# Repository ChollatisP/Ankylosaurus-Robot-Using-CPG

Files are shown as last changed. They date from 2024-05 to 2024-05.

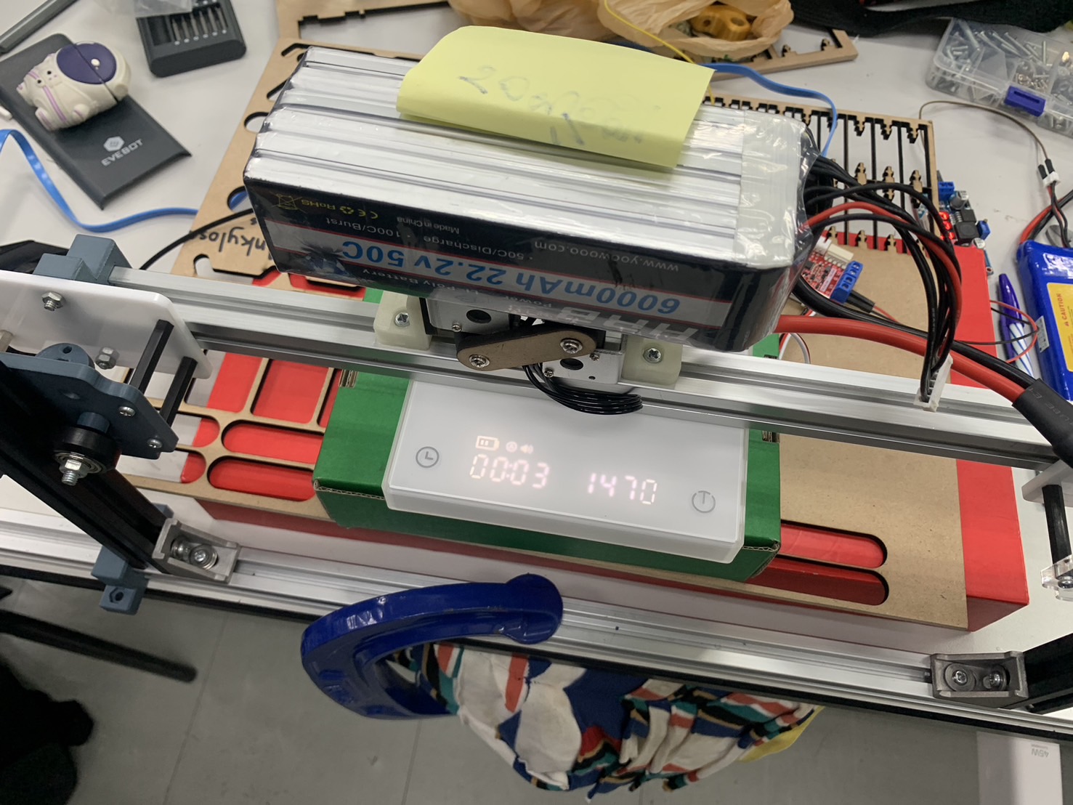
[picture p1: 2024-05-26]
Prove/Weight_test.jpg

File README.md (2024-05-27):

# Ankylosaurus Robot

## Description

The goal of this Mini-Project is to design and develop a robotic system inspired by the Ankylosaurus, an armored dinosaur. This robot will utilize a Central Pattern Generator (CPG), Virtual Rhythmic Networks (VRNs), and Virtual Hormones to simulate the nervous system found in living organisms. 

## Table of Content
- Ankylosaurus-Robot-Using-CPG
  - Description
  - Table of Content
  - Concept
    - Hormone
    - CPG-VRN
    - Robot design
  - Part
    - Tail
    - Neck-Head
    - Body
    - Left-Rear-Leg
    - Right-Rear-Leg
    - Left-Front-Leg
    - Right-Front-Leg
  - Assembly
  - Component
    - Software
    - Hardware
    - Installation
  - Authors
  - Acknowledgments
    - Manual and Datasheet
    - Reference

## Concept

### - CPG and VRN

<p align="center">
  
</p>
  
The robotic system, inspired by an ankylosaurus, features shoulder joints (M0-M3) and knee joints (M4-M7). SO2 is employed with O1 and O2 as outputs. Output from O1 controls knee joints, with weights of 1 and -1 causing Front Left and Rear Right knees to move in sync, while Front Right and Rear Left knees move oppositely, mimicking ankylosaurus limb coordination. Additionally, output from O2 is combined with Input 1 and 2 to allow inputs to influence shoulder movement, termed VRNs (Variable Response Networks), enabling input values to affect robot motion. 

### - Hormone

<p align="center">
  
</p>

In our hormone system, we use the motor torque to represent the robot's fatigue. We calculate the sum of the servo torque over five time windows and determine the standard deviation (SD) of this torque. This SD is then used in the hormone equation:

Hc[t]=(a⋅SD(Torque))+(b⋅Hc[t−1])

where 
a (alpha) and 
b (beta) are constants. The output 
Hc from this equation is used to adjust the motor speed. This system allows the hormone levels to influence the walking speed of the robot.

### - Robot design

* Materials and Equipment
  - PLA
  - Acrylic,2 mm and 4 mm
  - Wooden board 4 mm
  - Bearing(623RS) 3 mm
  - Screw
  - Nut
  - Inner tube
  - PVC pipe

* Body
  * Reference
    <p align="center">
      
    </p>

  * After choosing the Ankylosaurus as a reference for our robot, we based our design on a four-legged animal. Studying the skeleton of the Ankylosaurus, which has different leg lengths, we designed the front legs to be 86 centimeters long and the rear legs to be 115 centimeters long.

  * Free body diagram and Calculate force max in the home position. [Click hear](https://github.com/ChollatisP/Ankylosaurus-Robot-Using-CPG/blob/main/Prove/Free_body_diagram.pdf)
  * Experiment
    * Design testing showed that one leg can support 1500 grams, allowing the robot to support a total weight of 3000 grams with two legs. The robot's overall weight is approximately 1500 grams, with a tolerance of up to 50 percent (or 1500 grams). [Click hear](https://github.com/ChollatisP/Ankylosaurus-Robot-Using-CPG/blob/main/Prove/Experiment.mp4)
    * Energy consumption. [Click hear](https://github.com/ChollatisP/Ankylosaurus-Robot-Using-CPG/blob/main/Prove/Battery_Calculation.pdf)

* Tail
  * Reference
    <p align="center">
      
      
    </p>
    
  * We design 3D-printable joints for assembling a tail using PLA filament, with a total weight of 36 grams. Drawing inspiration from dragon models, the joints feature a grab mechanism, enabling the tail to move left and right.

* Head
  * Reference
    <p align="center">
      
      
    </p>

  * We designed the head structure based on Ankylosaurus anatomy. Its structure is similar to that of a turtle. But it has sharp spines and bone-like armor to protect it from predators. We also designed the mouth to have a jaw-like structure. This allows the servo to control the movement of the mouth. It also has a long neck so that the servo can move the neck up and down.

## Part

### - Tail

<p align="center">
  
</p>

### - Neck-Head

https://github.com/ChollatisP/Ankylosaurus-Robot-Using-CPG/assets/154317545/061143af-20ef-42ed-8587-2f487bc01352

### - Body

https://github.com/ChollatisP/Ankylosaurus-Robot-Using-CPG/assets/154317545/31a39d6f-0629-42f6-9094-0288651878a0

### - Left-Rear-Leg

https://github.com/ChollatisP/Ankylosaurus-Robot-Using-CPG/assets/154317545/f0d755fc-a621-4187-81f4-3e616c87f374

### - Right-Rear-Leg

https://github.com/ChollatisP/Ankylosaurus-Robot-Using-CPG/assets/154317545/73323a92-11e0-47a3-b45a-8f9a36d1330e

### - Left-Front-Leg

https://github.com/ChollatisP/Ankylosaurus-Robot-Using-CPG/assets/154317545/a362d214-d938-400e-98b1-ab38c1122920

### - Right-Front-Leg

https://github.com/ChollatisP/Ankylosaurus-Robot-Using-CPG/assets/154317545/f60c23ce-5cd6-48cf-a238-8bfbbe61a805

## Assembly

https://github.com/ChollatisP/Ankylosaurus-Robot-Using-CPG/assets/154317545/6cbdc5d4-3189-4b34-b544-ea275060897f

## Component

### - Software

* [Arduino IDE](https://www.arduino.cc/en/software) (Any version)
  * Library
    * Normal
      * math.h
      * WiFi.h
      * PubSubClient.h
      * ESP32Servo.h
      * [How to install arduino library](https://support.arduino.cc/hc/en-us/articles/5145457742236-Add-libraries-to-Arduino-IDE) 

    * Additional

      * [SCS15 Servo arduino driver](https://github.com/IS2511/SCServo.git)

      * [How to install additional arduino library](https://docs.arduino.cc/software/ide-v1/tutorials/installing-libraries/)  

* SOLIDWORKS or Fusion 360 or any cad design software.

* RDWorksV8 (Laser Cut and Engrave Software)

* PrusaSlicer (Up to your 3D printer)

* [Node-RED](https://www.influxdata.com/blog/guide-installing-node-red/)
  * [Palette node-red-dashboard](https://www.influxdata.com/blog/node-red-dashboard-tutorial/)

* [FD 1.9.8.2](https://github.com/ChollatisP/Ankylosaurus-Robot-Using-CPG/tree/main/Feetech%20SCSservo%20Software) (SCSservo Software)

### - Hardware

* Feetech SCS15 Motor 
   * quantity 8
 * FE-URT-1 
   * quantity 1
 * Step Down (LM2596) 
   * quantity 1
 * MG90S Servo Motor 
   * quantity 2
 * Arduimo UNO R4 WIFI 
   * quantity 1
 * Node32S
   * quantity 1
 * Photo Board (8.5*5.5 cm.)
   * quantity 1
 * 3000 mAh Li-Po Battery
   * quantity 1
 * Jumper wire

### - Diagram & Wiring

<p align="center">
  
  
</p>

### - Installation

<p align="center">
  
</p>

## Group members 

* Nipitpon Phumchoedchan 6452500015

* Chollatis Petchsing 6452500023

* Akaraphon Trakoolwiya 6452500180

* Kantawit Panyateang 6452500198

* Wiraphat panma 6452500350

* Komgrid Petchpayub 6452500392

## Acknowledgments
### - Manual and Datasheet

* [Arduino® UNO R4 WiFi](https://docs.arduino.cc/resources/datasheets/ABX00087-datasheet.pdf)

* [Servo motor SCS 15](https://www.feetechrc.com/Data/feetechrc/upload/file/20201127/start%20%20tutorial201015.pdf)

* [Servo motor SCS 15 manual](https://grobotronics.com/images/companies/1/datasheets/SCS15&SCS115%20Manual.pdf?1516269264467)

* [FE-URT-1](https://www.mantech.co.za/datasheets/products/FE-URT-1%20specs.pdf)

* [Step Down (LM2596)](https://www.ti.com/lit/ds/symlink/lm2596.pdf)

* [MG90S Servo Motor](https://www.electronicoscaldas.com/datasheet/MG90S_Tower-Pro.pdf)

* [Node32S](https://www.es.co.th/Schemetic/PDF/ESP32.PDF)

### - [Reference](https://github.com/ChollatisP/Ankylosaurus-Robot-Using-CPG/tree/main/Reference)

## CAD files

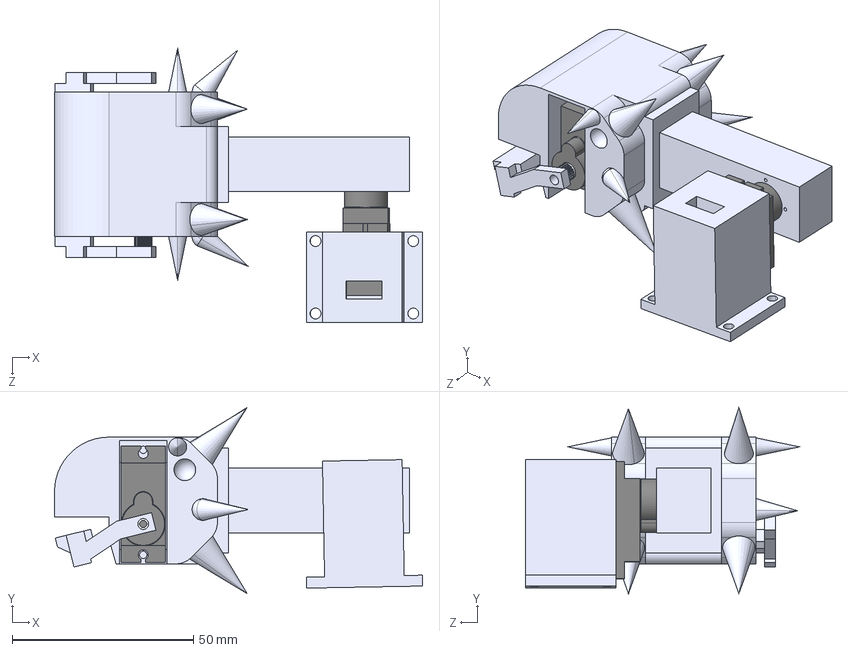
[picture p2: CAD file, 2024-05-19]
CAD/File step/HEAD/Assembly.STEP
101.6 x 51.5 x 75.7 mm
MG90S Servo Motor.stp x 2

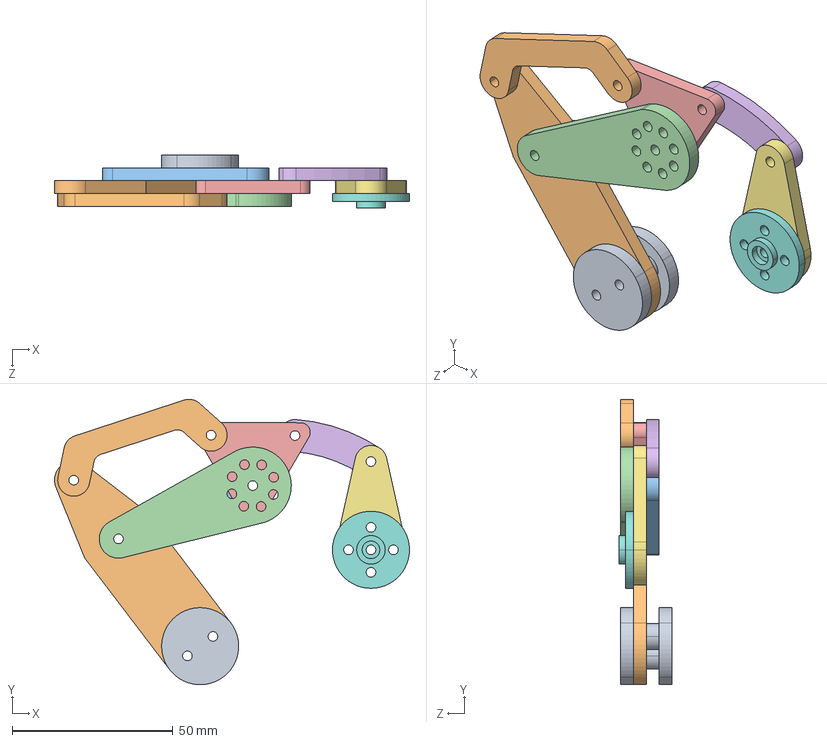
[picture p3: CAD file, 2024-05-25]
CAD/File step/Legs/Front legs/Assembly Right.STEP
110.6 x 88.9 x 16.5 mm
back10.step x 2
front1.step
front2.step
front4.step
front5.step
front6.step
front7.step
front8.step
front9.step x 2
front3.step

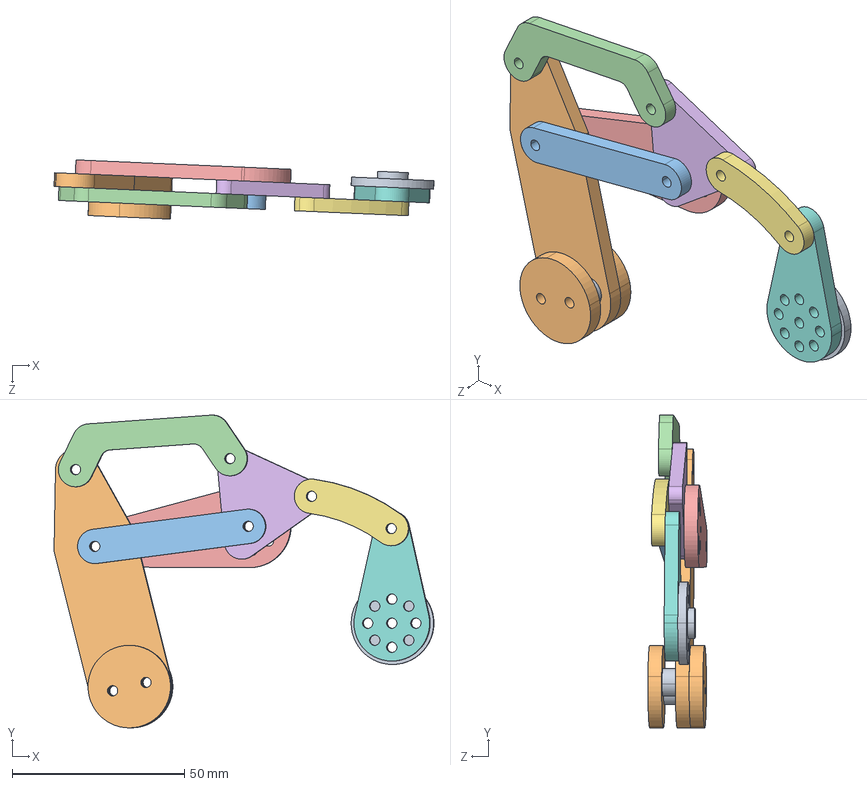
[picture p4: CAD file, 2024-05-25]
CAD/File step/Legs/Front legs/Assembly Left.STEP
110.4 x 90.9 x 17.2 mm
back10.step x 2
front1.step
front2.step
front3.step
front4.step
front5.step
front6.step
front7.step
front8.step
front9.step x 2

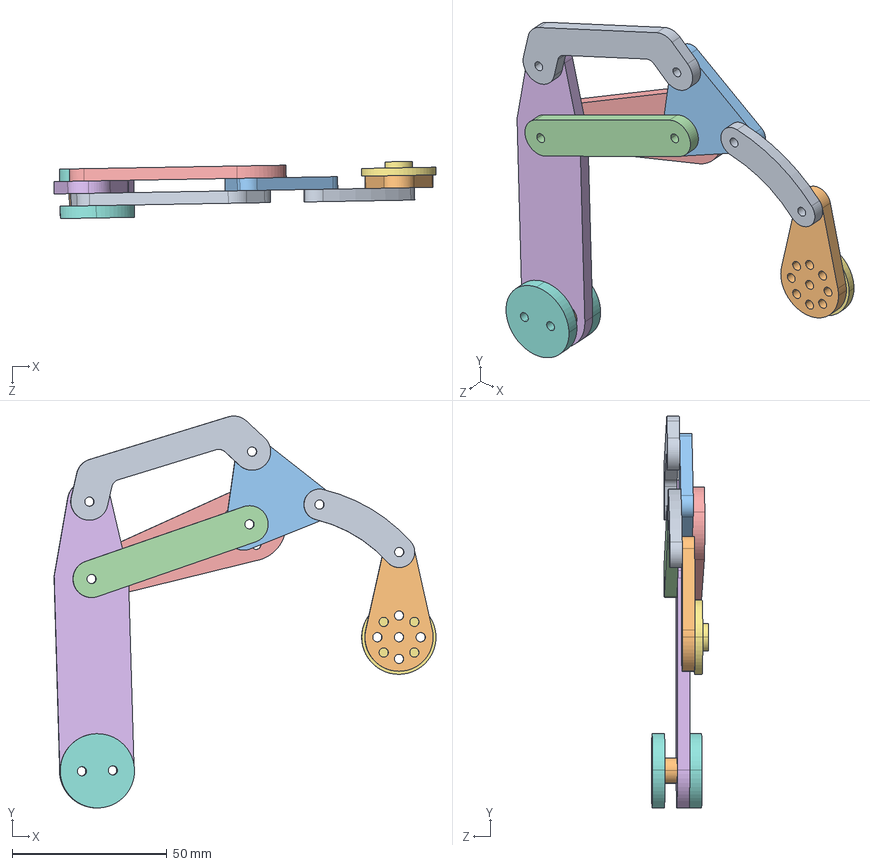
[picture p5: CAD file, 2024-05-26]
CAD/File step/Legs/Rear legs/Assembly Left.STEP
123.4 x 126.6 x 18.5 mm
back1.step
back10.step x 2
back2.step
back3.step
back4.step
back5.step
back6.step
back7.step x 2
back8.step
back9.step

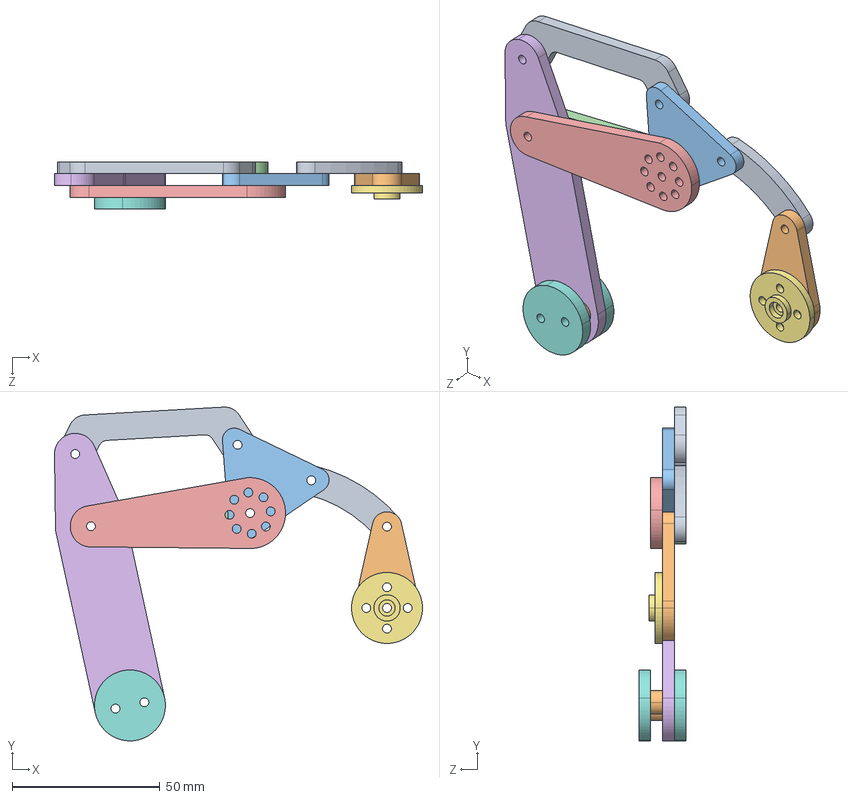
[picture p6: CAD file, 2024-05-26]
CAD/File step/Legs/Rear legs/Assembly Right.STEP
124.4 x 112.9 x 16.0 mm
back1.step
back10.step x 2
back2.step
back3.step
back4.step
back5.step
back6.step
back7.step x 2
back8.step
back9.step

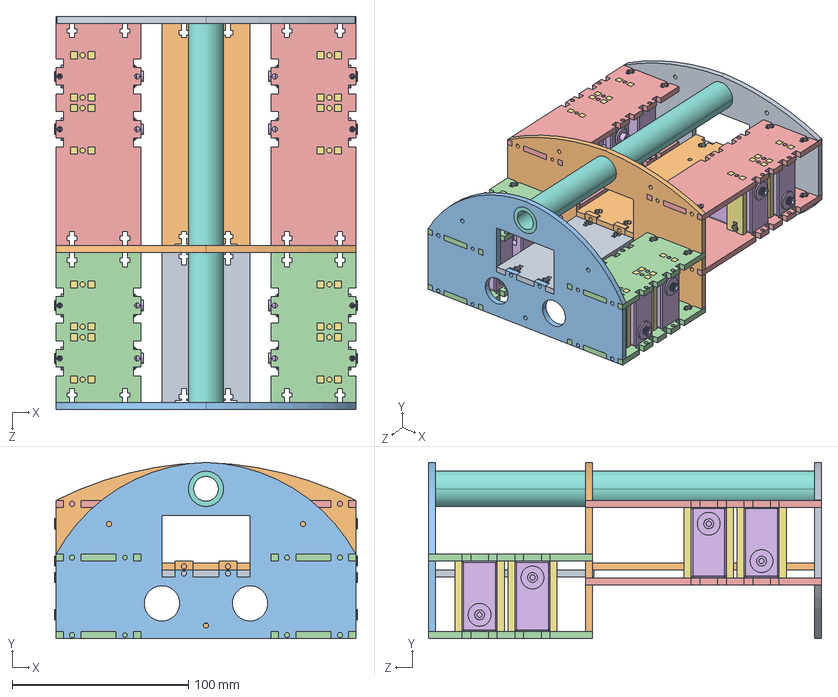
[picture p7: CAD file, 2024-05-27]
CAD/File step/BODY/BodyAssembly.STEP
172.0 x 100.0 x 223.0 mm
หลัง2.4.2
หลัง2.4
หลัง3
servoscs15.step x 8
เเนบมอเตอร์ x 16
ตรงกลาง
ตรงกลาง2.1

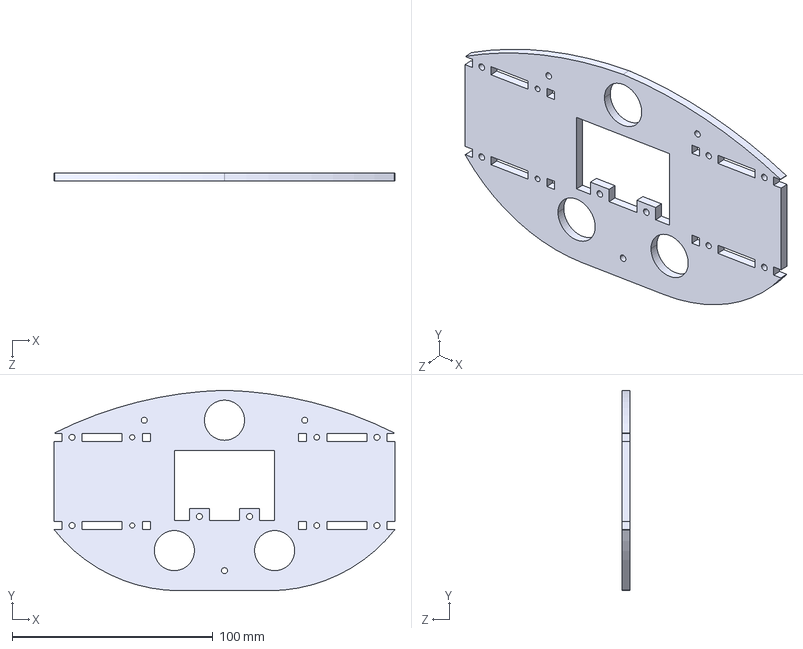
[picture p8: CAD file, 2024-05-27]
CAD/File step/BODY/BODY_PART7.STEP
170.0 x 99.9 x 4.00 mm

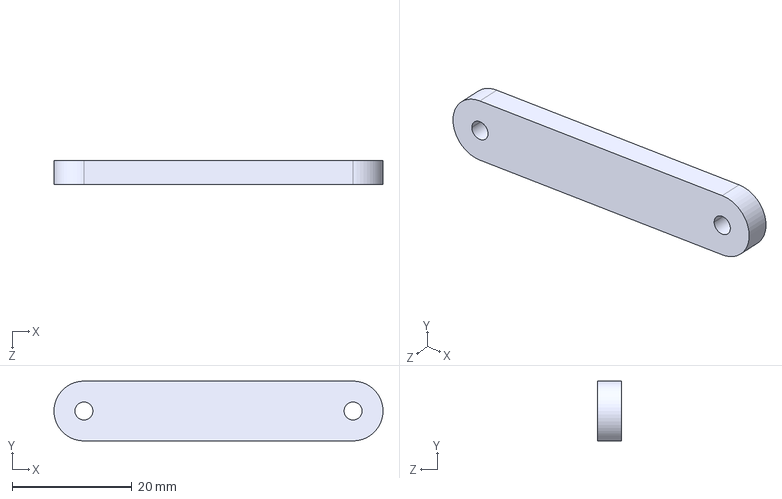
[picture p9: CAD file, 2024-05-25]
CAD/File step/Legs/Front legs/front2.STEP
55.0 x 10.0 x 4.00 mm

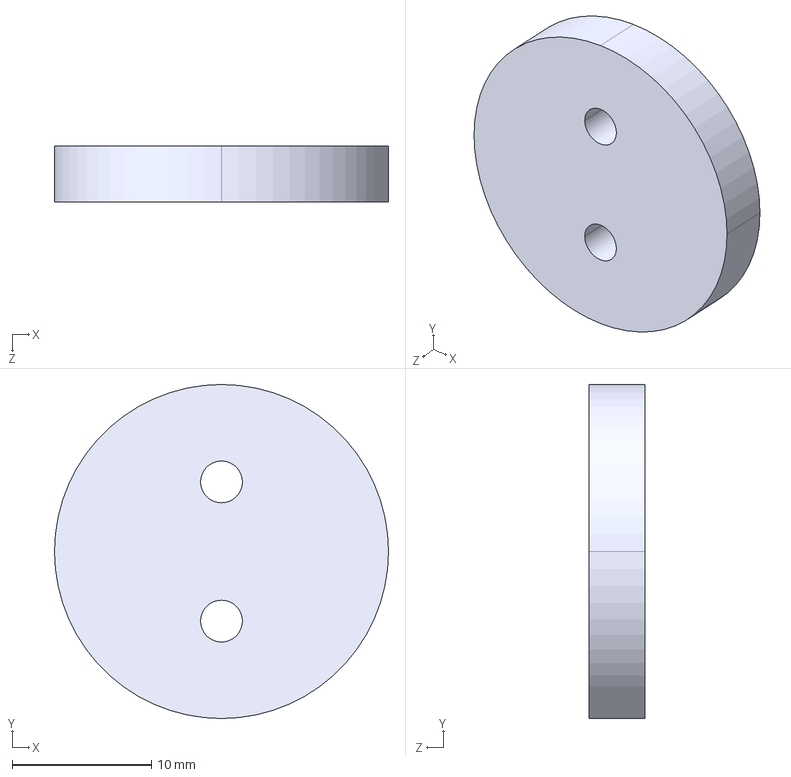
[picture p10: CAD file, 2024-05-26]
CAD/File step/Legs/Rear legs/back7.STEP
24.0 x 24.0 x 4.00 mm

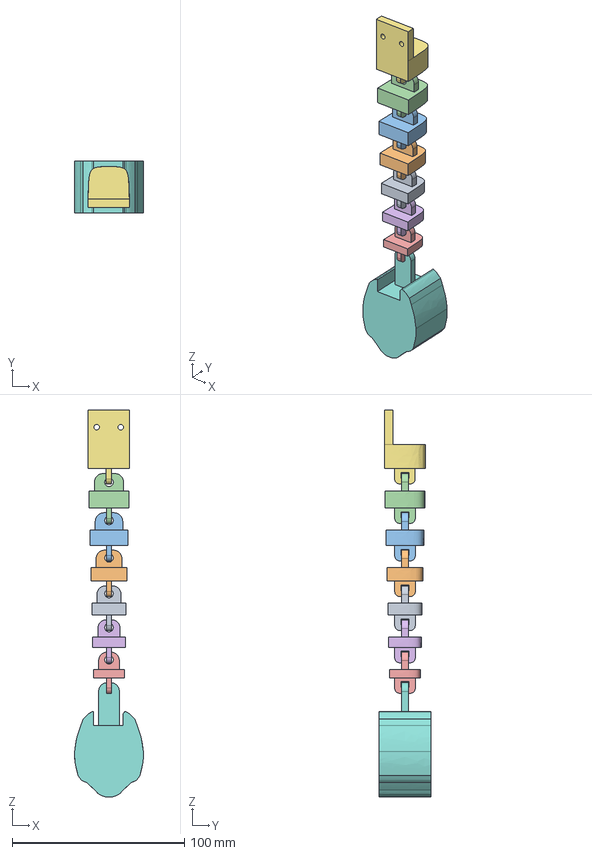
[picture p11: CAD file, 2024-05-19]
CAD/File step/Tail.step
40.0 x 30.0 x 225.0 mm
Test more3
Test more2
Test more1
Test more0
Test more5
Test more4
Test more0.1
Big

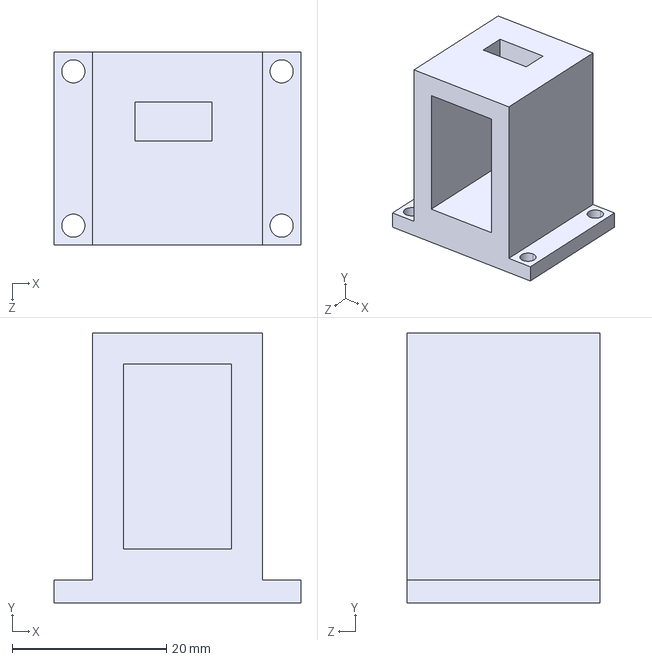
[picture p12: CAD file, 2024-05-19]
CAD/File step/HEAD/Part3.STEP
32.0 x 35.0 x 25.0 mm

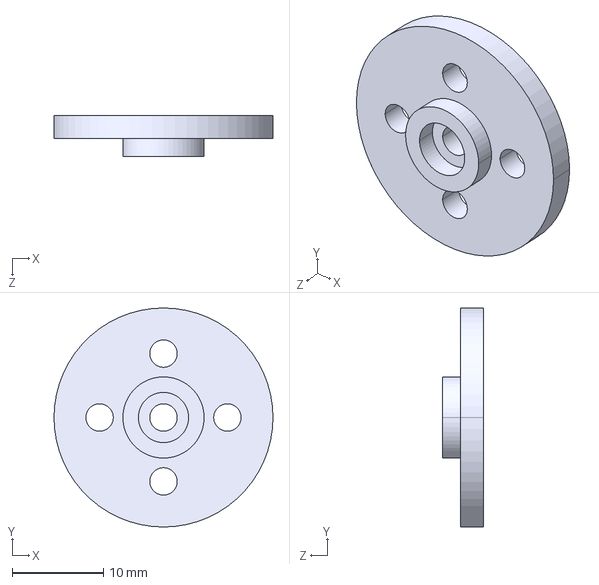
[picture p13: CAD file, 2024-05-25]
CAD/File step/Legs/Front legs/front8.STEP
24.0 x 24.0 x 4.50 mm

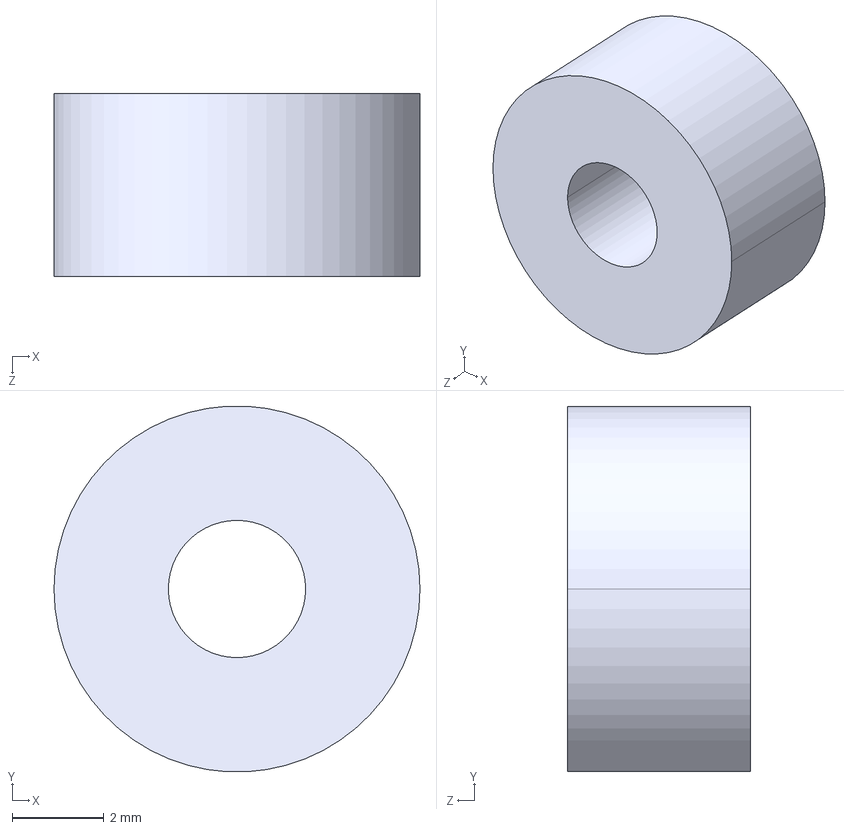
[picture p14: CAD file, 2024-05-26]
CAD/File step/Legs/Rear legs/back10.STEP
8.00 x 7.99 x 4.00 mm

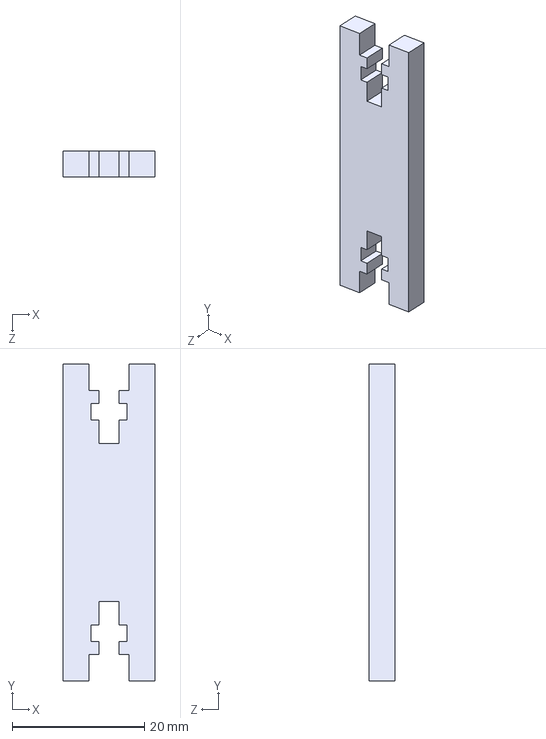
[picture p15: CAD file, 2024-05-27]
CAD/File step/BODY/BODY_PART9.STEP
14.0 x 48.0 x 4.00 mm

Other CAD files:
CAD/File step/BODY/BODY_PART3.STEP
CAD/File step/HEAD/Part5.STEP
CAD/File step/Legs/Rear legs/back1.STEP
CAD/File step/BODY/BODY_PART6.STEP
CAD/File step/BODY/BODY_PART1.STEP
CAD/File step/BODY/BODY_PART2.STEP
CAD/File step/BODY/BODY_PART4.STEP
CAD/File step/BODY/BODY_PART5.STEP
CAD/File step/BODY/BODY_PART8.STEP
CAD/File step/HEAD/Part1.STEP
CAD/File step/HEAD/Part2.STEP
CAD/File step/HEAD/Part6.STEP
CAD/File step/Legs/Front legs/front1.STEP
CAD/File step/Legs/Front legs/front10.STEP
CAD/File step/Legs/Front legs/front3.STEP
CAD/File step/Legs/Front legs/front4.STEP
CAD/File step/Legs/Front legs/front5.STEP
CAD/File step/Legs/Front legs/front6.STEP
CAD/File step/Legs/Front legs/front7.STEP
CAD/File step/Legs/Front legs/front9.STEP
CAD/File step/Legs/Rear legs/back2.STEP
CAD/File step/Legs/Rear legs/back3.STEP
CAD/File step/Legs/Rear legs/back4.STEP
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

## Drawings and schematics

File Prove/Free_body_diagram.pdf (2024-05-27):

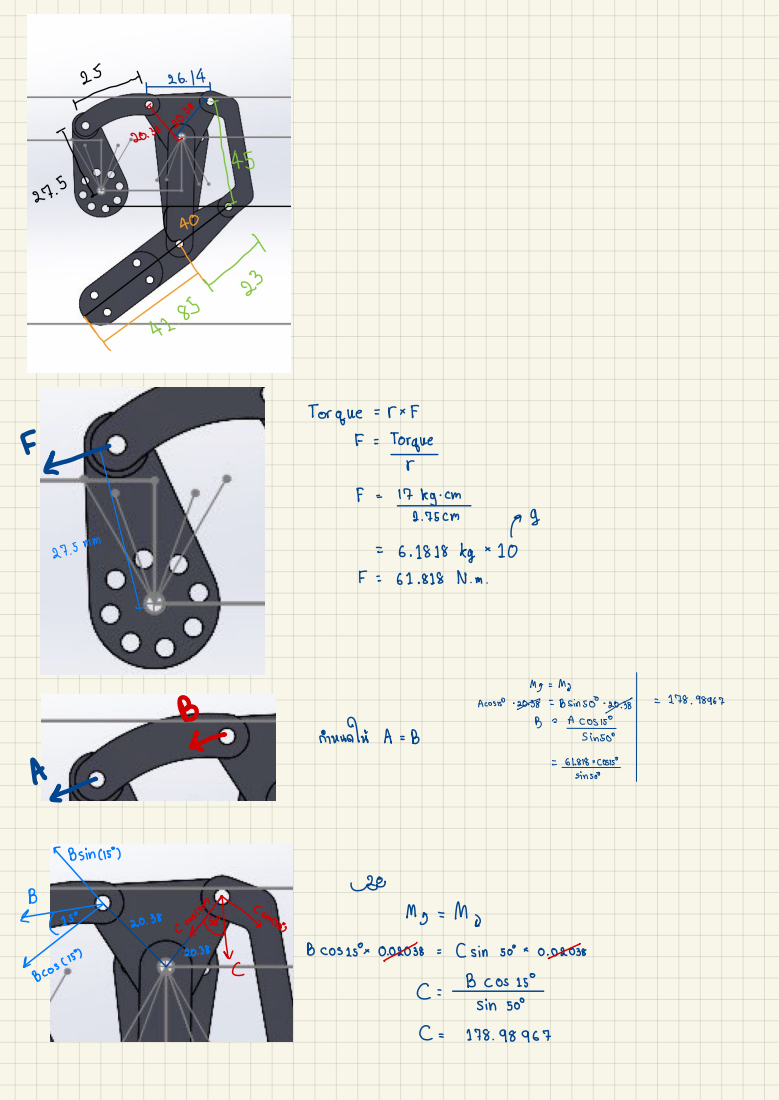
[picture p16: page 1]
Torque =; Torque; F = ·17 Reg. cm; A cOSISO; ·8 = BSinsoO :; กำหนดให้ A =; B = A COSISO; SinSor; - COSISO ↑; sin 50; 5 BSin C15; Sinceo 20.38; COS15,; 0.02038 = ( sin; cos (¹⁵; BCos 13; sin

# Ma = MG

CSinsox0.023 = | Dxsin | 15 x 0.04185

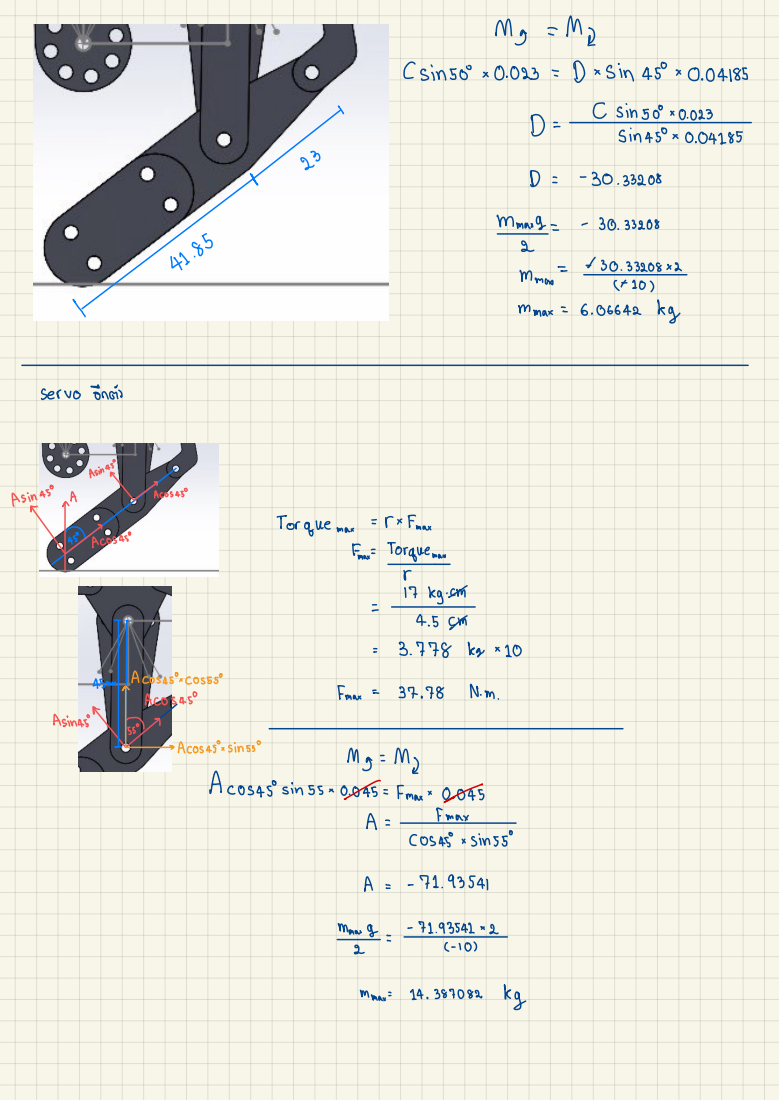
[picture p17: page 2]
sin 500 -; Sin 450 -; - 30.33208 uss "; mmax8 =; mmox; mmax =; servo อีกต; Asin " cos4s Asin ⁴⁵·A ↑; Accos 49; Torque max =; Ux Fmax; Emax =; Torque max; keg. =; ACOS450 , COS550 ค; ACOS 45; Frax =; Asinas &; · ACOS45-; sings; Mar = MG; ACOS4S sin 5 3 -; 0 = Fmax - 0.045 -; I max; COS45 + Sins %; mmas 8 -=; mmax=

| 30 | -
↳ | (25% | 23.48 %

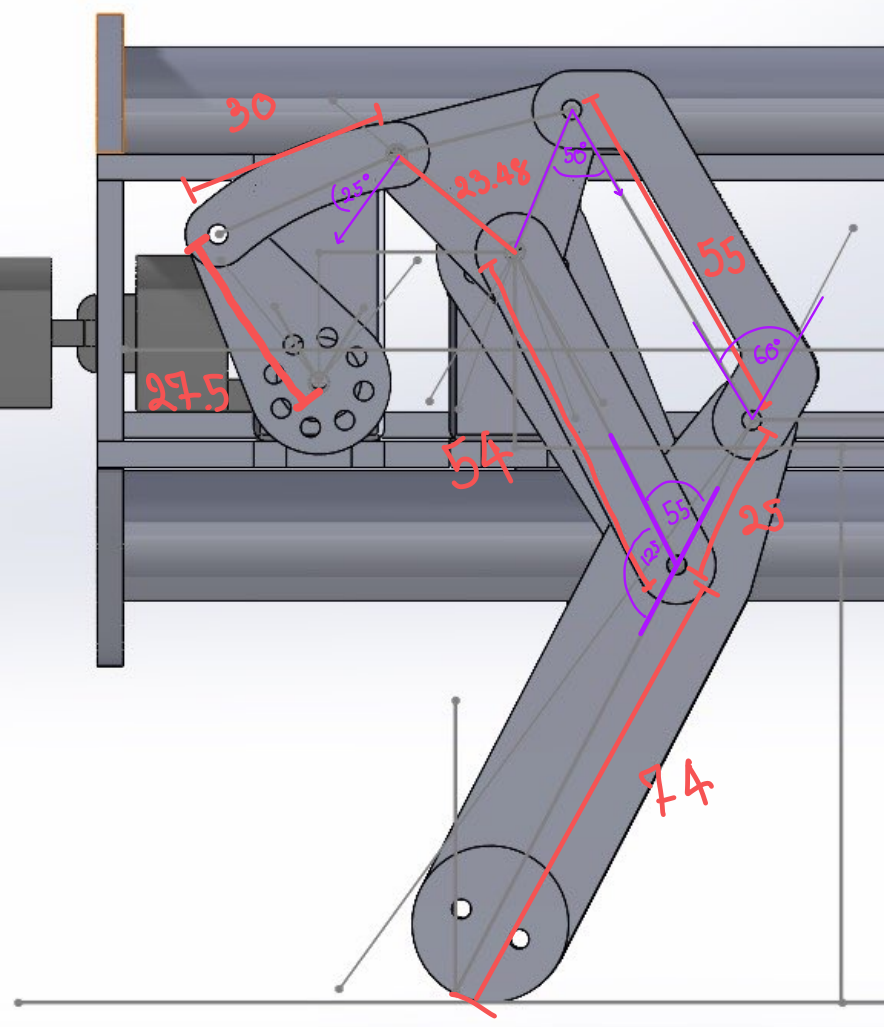
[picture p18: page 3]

MACOSASO รีว | docos | 8Bsin40
pr | -

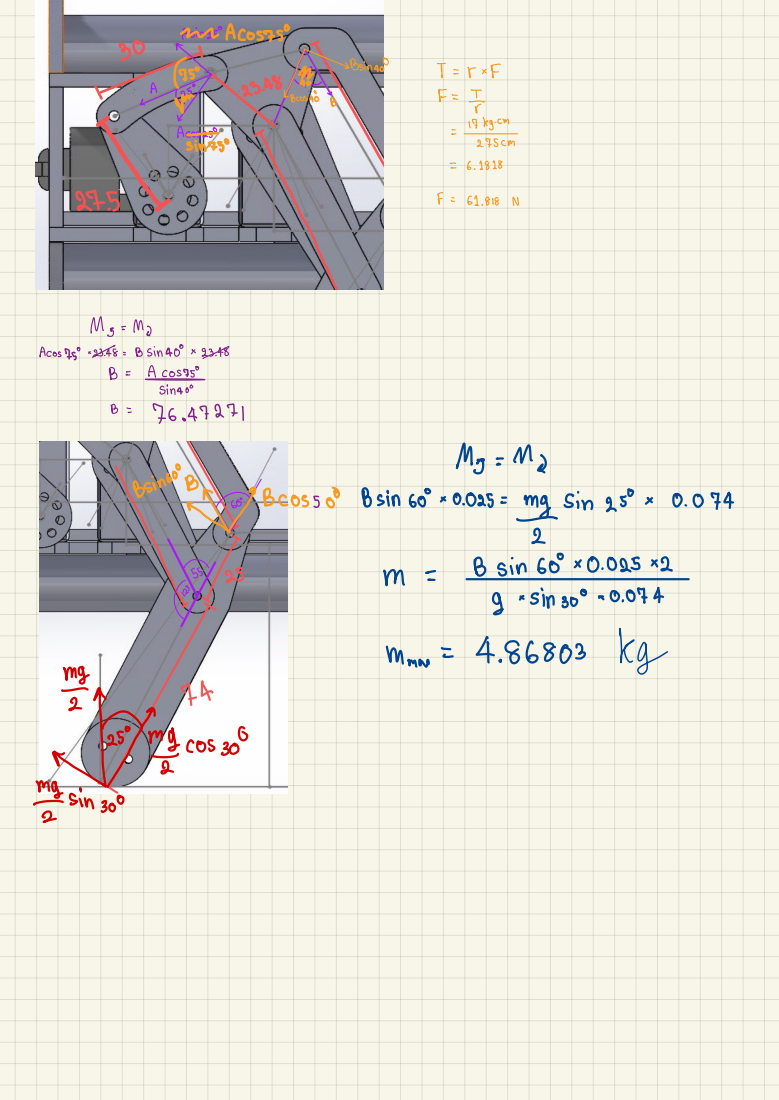
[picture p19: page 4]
AcOS258; Sin750; Acosts48; Sin 40; ACOSISO; Sin4 0; sins" · BCOS5 8; Basin; 60 - 0.025 : # sin; BSin; &sin 300 - ⁰.07 4; Mama =; #comp ↑; cos; #O sin so·

# T = U x f

## macOS400 F = ②

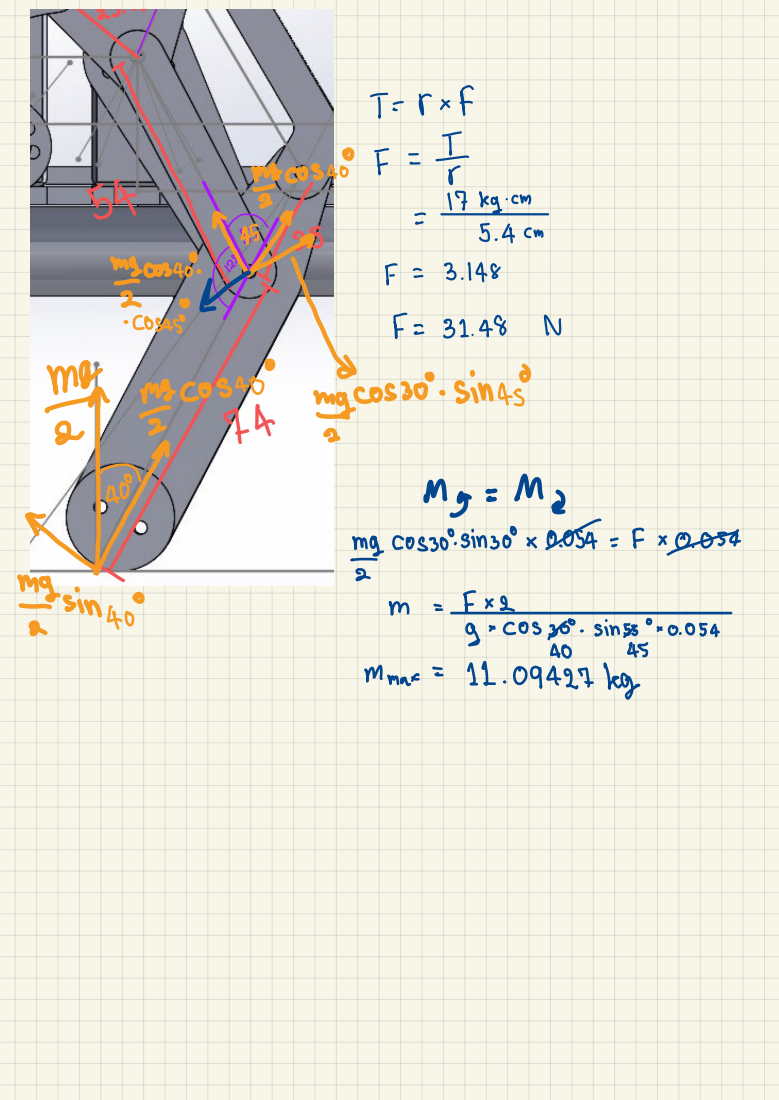
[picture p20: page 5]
=17 Reg. cr; mecos⁴·; บ · COS430; #210530. sinks; #smacosi 2; my cos30sin30 x 0.054 = Fx↳; musin; 9 - COS /; 30. Sin55 - 0.054; Mamax =; Leg

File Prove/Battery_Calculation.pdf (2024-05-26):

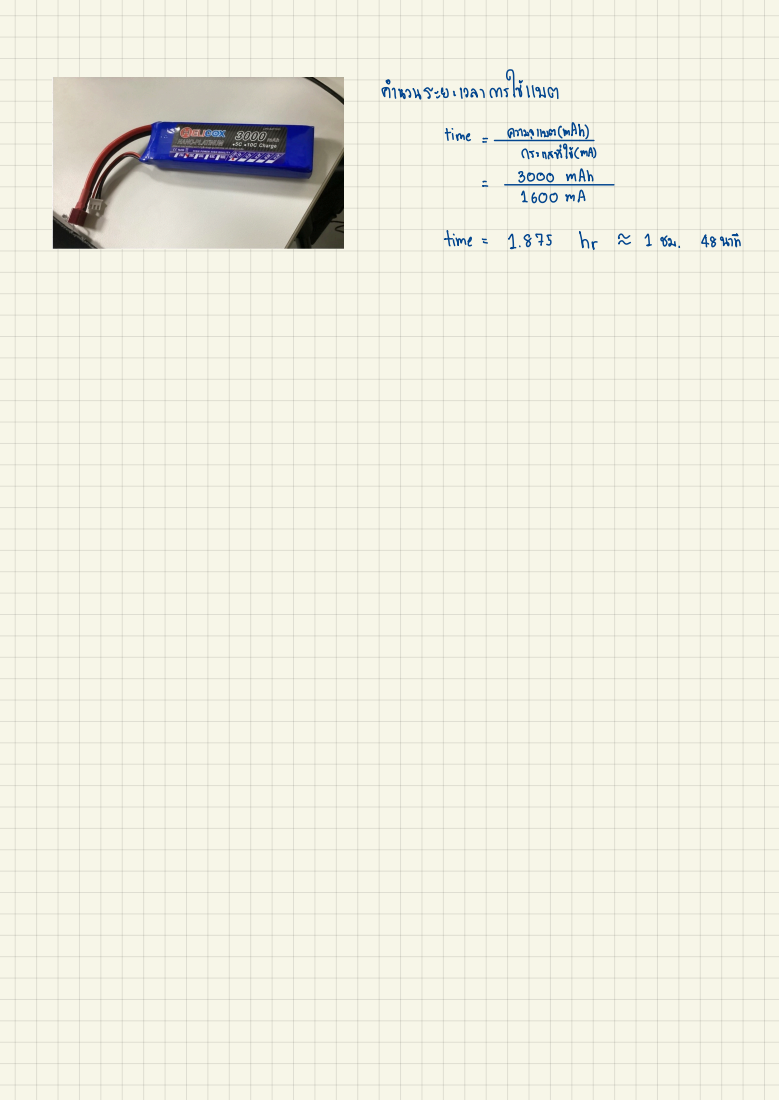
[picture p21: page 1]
ตตำ นวนระยะเวลาการใใช้แ; time =; ความจแบต(MAh; กระแสทที่ใช้ (; 3000 mAh =; time = 1.875 hr. ~ 1; 48 นาท

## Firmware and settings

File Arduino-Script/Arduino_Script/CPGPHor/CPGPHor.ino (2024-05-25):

#include<math.h>
#include <SCServo.h>
#define GPIO_PIN_1 7 // กำหนดหมายเลขของ GPIO ที่ต้องการใช้รับข้อมูล 1
#define GPIO_PIN_2 4 // กำหนดหมายเลขของ GPIO ที่ต้องการใช้รับข้อมูล 2
SCSCL sc;

float MI = 0.1;
#define Alpha 1.01
#define phi M_PI/6
float speed = 700 ;
const int arraySize = 9;
float sensorValues[arraySize];
float sensorValues2[arraySize];
int currentIndex = 0;
int currentIndex1 = 0;
float Hc[2] = {0, 0};
float Hc2[2] = {0, 0};
const long interval12 = 250; 
const long interval1 = 250; 
unsigned long previousMillis12 = 0;
unsigned long previousMillis1 = 0;
//----------W_for_CPG--------//
/*#define w11 1.5//Alpha*(cos(phi+MI))//1.5
#define w22 1.5//Alpha*(cos(phi+MI))//1.5
#define w12 -(0.4+MI)//Alpha*(-sin(phi+MI))//-(0.6+MI)
#define w21 0.4+MI//Alpha*(sin(phi+MI))//0.6+MI
*/
float w11 = Alpha*(cos(phi+MI));//1.5
float w22 = Alpha*(cos(phi+MI));//1.5
float w12 = Alpha*(-sin(phi+MI));//-(0.6+MI)
float w21 = Alpha*(sin(phi+MI));//0.6+MI
#define w_for_C3579_and_o2 1.7246
#define w_for_C46810_and_o2 -1.7246
#define w_for_C36710_and_oinput 1.7246
#define w_for_C4589_and_oinput -1.7246
#define w_for_C11and12minus -0.5
#define w_for_C11and12plus 0.5

#define C1 0.5
#define C2 0.5
#define BIAS -2.48285
#define CPG_BIAS 0.01
#define Motor_4to7_Bias -0.5

//-----------W_for_M------------//
#define weight_for_M_4and7 -1
#define weight_for_M_5and6 1
#define weight_for_M_0and3 -1.3
#define weight_for_M_1and2 1.3

//------------MinMaxforMotor------------//
/*#define M0_MAX 0.774393239//0.15
#define M0_MIN -0.775747801//-0.2
#define M1_MAX 0.775747801//0.2
#define M1_MIN -0.774393239//-0.15
#define M2_MAX 0.418318016//0.2
#define M2_MIN 0.367229335//-0.2
#define M3_MAX -0.367229335//0.2
#define M3_MIN -0.418318016//-0.2
#define M4_MAX 0.425807758//-0.3
#define M4_MIN -1.430628636//-0.7
#define M5_MAX 0.430628636//-0.3
#define M5_MIN -1.425807758//-0.7
#define M6_MAX 0.430628636//-0.3
#define M6_MIN -1.425807758//-0.7
#define M7_MAX 0.425807758//-0.3
#define M7_MIN -1.430628636//-0.7

*/
#define M0_MAX 0.15
#define M0_MIN -0.2
#define M1_MAX 0.2
#define M1_MIN -0.15
#define M2_MAX 0.2
#define M2_MIN -0.2
#define M3_MAX 0.2
#define M3_MIN -0.2
#define M4_MAX 0-0.3
#define M4_MIN -0.7
#define M5_MAX -0.3
#define M5_MIN -0.7
#define M6_MAX -0.3
#define M6_MIN -0.7
#define M7_MAX -0.3
#define M7_MIN -0.7

int INPUT1 = -2;
int INPUT2 = 1;
float O_INTPUT1 = tanh(INPUT1);
float O_INTPUT2 = tanh(INPUT2);

//----------CPG-Value---------//
float Current_C1_Values;
float Current_C2_Values;
float Current_O1_Values;
float Current_O2_Values;
float Prev_C1_Values;
float Prev_C2_Values;
float Prev_O1_Values;
float Prev_O2_Values;
float C3_Values;
float C4_Values;
float C5_Values;
float C6_Values;
float C7_Values;
float C8_Values;
float C9_Values;
float C10_Values;
float C11_Values;
float C12_Values;
float O3_Values;
float O4_Values;
float O5_Values;
float O6_Values;
float O7_Values;
float O8_Values;
float O9_Values;
float O10_Values;
float O11_Values;
float O12_Values;

//---------Motor_home_positon---------//
#define M0_Home 420
#define M1_Home 400
#define M2_Home 500
#define M3_Home 600
#define M4_Home 520
#define M5_Home 450
#define M6_Home 600
#define M7_Home 520


//------------Motor_define_shoulder-----------//
#define M0 12
#define M1 7
#define M2 9
#define M3 6
//------------Motor_define_foot-----------//
#define M4 11
#define M5 8
#define M6 10
#define M7 5

/*
#define M4 12
#define M5 7
#define M6 9
#define M7 6
//------------Motor_define_foot-----------//
#define M0 11
#define M1 8
#define M2 10
#define M3 5
*/
//--------------Motor_value--------------//
float M0val,M1val,M2val,M3val,M4val,M5val,M6val,M7val;

//----------Motor-limitation---------------//
//ขาหน้าขวา
#define MIN_ID11 360 //ยกขาลง
#define MAX_ID11 560  //ยกขาขึ้น
#define MIN_ID12 420 //ก้าวขาหน้า
#define MAX_ID12 520  //ก้าวขาถอย

//ขาหน้าซ้าย
#define MIN_ID9 500//ยกขาลง
#define MAX_ID9 600//ยกขาขึ้น
#define MIN_ID10 500  //ก้าวขาถอย
#define MAX_ID10 700  //ก้าวขาหน้า

//ขาหลังขวา
#define MIN_ID7 382 //ยกขาลงสุด
#define MAX_ID7 582 //ยกขาขึ้นสุด
#define MIN_ID8 540 //ก้าวขาหน้า(เดินหน้า) 152-342
#define MAX_ID8 340 //ก้าวขาถอยหลัง(ถอยหลัง)

//ขาหลังซ้าย
#define MIN_ID5 650  //ยกขาขึ้น
#define MAX_ID5 450 //ยกขาลง
#define MIN_ID6 400 //ก้าวขาถอย
#define MAX_ID6 600  //ก้าวขาหน้า

void setup() 
{
  Serial.begin(115200);

   for (int i = 0; i < arraySize; i++) {
    sensorValues[i] = 0;
  }
  pinMode(GPIO_PIN_1, INPUT); // กำหนด GPIO เป็นโหมด INPUT
  pinMode(GPIO_PIN_2, INPUT); // กำหนด GPIO เป็นโหมด INPUT
  Serial.println("Start");
  Serial1.begin(1000000);
  sc.pSerial = &Serial1;
  Prev_C1_Values = C1;
  Prev_O1_Values = tanh(Prev_C1_Values);
  Prev_C2_Values = C2;
  Prev_O2_Values = tanh(Prev_C2_Values);
  sc.RegWritePos(M0,M0_Home,0,1000);
  sc.RegWritePos(M1,M1_Home,0,1000);
  sc.RegWritePos(M2,M2_Home,0,1000);
  sc.RegWritePos(M3,M3_Home,0,1000);
  sc.RegWritePos(M4,M4_Home,0,1000);
  sc.RegWritePos(M5,M5_Home,0,1000);
  sc.RegWritePos(M6,M6_Home,0,1000);
  sc.RegWritePos(M7,M7_Home,0,1000);
  sc.RegWriteAction();
  delay(1000);
}

float map(float x, float in_min, float in_max, float out_min, float out_max) {
  return (x - in_min) * (out_max - out_min) / (in_max - in_min) + out_min;
}

//int i=0;
void loop() 
{
  CPGLOOP();
  int data_1 = digitalRead(GPIO_PIN_1);
  // ส่งข้อมูลที่รับไปทาง Serial
  //Serial.println(data_1);
  if(data_1 == 0)
  {
    speed = 1;
  }
}


void CPGLOOP()
{
  //Serial.println("Start");
  
  //-----------CPG----------------//
  Current_C1_Values = (Prev_O1_Values * w11) + (Prev_O2_Values * w21) + CPG_BIAS;
  Current_C2_Values = (Prev_O2_Values * w22) + (Prev_O1_Values * w12) + CPG_BIAS;

  Current_O1_Values = tanh(Current_C1_Values);
  Current_O2_Values = tanh(Current_C2_Values);
  
  C3_Values = (Current_O2_Values*w_for_C3579_and_o2)+(O_INTPUT2*w_for_C36710_and_oinput)+BIAS;
  C4_Values = (Current_O2_Values*w_for_C46810_and_o2)+(O_INTPUT2*w_for_C4589_and_oinput)+BIAS;
  C5_Values = (Current_O2_Values*w_for_C3579_and_o2)+(O_INTPUT2*w_for_C4589_and_oinput)+BIAS;
  C6_Values = (Current_O2_Values*w_for_C46810_and_o2)+(O_INTPUT2*w_for_C36710_and_oinput)+BIAS;
  C7_Values = (Current_O2_Values*w_for_C3579_and_o2)+(O_INTPUT2*w_for_C36710_and_oinput)+BIAS;
  C8_Values = (Current_O2_Values*w_for_C46810_and_o2)+(O_INTPUT2*w_for_C4589_and_oinput)+BIAS;
  C9_Values = (Current_O2_Values*w_for_C3579_and_o2)+(O_INTPUT2*w_for_C4589_and_oinput)+BIAS;
  C10_Values = (Current_O2_Values*w_for_C46810_and_o2)+(O_INTPUT2*w_for_C36710_and_oinput)+BIAS;
  O3_Values = tanh(C3_Values);
  O4_Values = tanh(C4_Values);
  O5_Values = tanh(C5_Values);
  O6_Values = tanh(C6_Values);
  O7_Values = tanh(C7_Values);
  O8_Values = tanh(C8_Values);
  O9_Values = tanh(C9_Values);
  O10_Values = tanh(C10_Values);  
  C11_Values = (w_for_C11and12plus*(O3_Values+O4_Values))+(w_for_C11and12minus*(O5_Values+O6_Values));
  C12_Values = (w_for_C11and12plus*(O7_Values+O8_Values))+(w_for_C11and12minus*(O9_Values+O10_Values));
  O11_Values = tanh(C11_Values);
  O12_Values = tanh(C12_Values); 
  M0val = (O11_Values*weight_for_M_0and3);
  M1val = (O11_Values*weight_for_M_1and2);
  M2val = (O12_Values*weight_for_M_1and2);
  M3val = (O12_Values*weight_for_M_0and3);
  M4val = (Current_O1_Values*weight_for_M_4and7)+Motor_4to7_Bias;
  M5val = (Current_O1_Values*weight_for_M_5and6)+Motor_4to7_Bias;
  M6val = (Current_O1_Values*weight_for_M_5and6)+Motor_4to7_Bias;
  M7val = (Current_O1_Values*weight_for_M_4and7)+Motor_4to7_Bias;
  mapmotor(M0val,M1val,M2val,M3val,M4val,M5val,M6val,M7val);
  delay(50);
  Prev_C1_Values = Current_C1_Values;
  Prev_O1_Values = Current_O1_Values;
  Prev_C2_Values = Current_C2_Values;
  Prev_O2_Values = Current_O2_Values;
}
void mapmotor(float M0val,float M1val,float M2val,float M3val,float M4val,float M5val,float M6val,float M7val)
{
  // Serial.print("M0:");
  // Serial.print(M0val , 7);
  // Serial.print("\tM1:");
  // Serial.print(M1val , 7);
  // Serial.print("\tM2:");
  // Serial.print(M2val , 7);
  // Serial.print("\tM3:");
  // Serial.print(M3val , 7);
  // Serial.print("\tM4:");
  // Serial.print(M4val , 7);
  // Serial.print("\tM5:");
  // Serial.print(M5val, 7);
  // Serial.print("\tM6:");
  // Serial.print(M6val, 7);
  // Serial.print("\tM7:");
  // Serial.println(M7val, 7);

  float posM0 = map(M0val, M0_MIN, M0_MAX, MAX_ID12, MIN_ID12);
  float posM4 = map(M4val, M4_MIN, M4_MAX, MAX_ID11, MIN_ID11);

  //ขาหลังขวา
  float posM1 = map(M1val, M1_MIN, M1_MAX, MIN_ID7, MAX_ID7);
  float posM5 = map(M5val, M5_MIN, M5_MAX, MIN_ID8, MAX_ID8);

  //ขาหน้าซ้าย
  float posM2 = map(M2val, M2_MIN, M2_MAX, MIN_ID9, MAX_ID9);
  float posM6 = map(M6val, M6_MIN, M6_MAX, MIN_ID10, MAX_ID10);

  //ขาหลังซ้าย
  float posM3 = map(M3val, M3_MIN, M3_MAX, MAX_ID6, MIN_ID6);
  float posM7 = map(M7val, M7_MIN, M7_MAX, MAX_ID5, MIN_ID5);

  // sc.WritePos(11,pos11,0,1500);
  sc.WritePos(M0,posM0,0,speed);
  sc.WritePos(M1,posM1,0,speed);
  sc.WritePos(M2,posM2,0,speed);
  sc.WritePos(M3,posM3,0,speed);
  sc.WritePos(M4,posM4,0,speed);
  sc.WritePos(M5,posM5,0,speed);
  sc.WritePos(M6,posM6,0,speed);
  sc.WritePos(M7,posM7,0,speed);
  //Serial.print("  Torqe:");
  //Serial.println(sumofload());
  sumofload();
}
int sumofload()
{
  int Torqe[7];
  int Torqe_total=0;
  for (int j=0 ;j <=7;j++)
  {
    Torqe[j]=abs(sc.ReadLoad(5+j));
    Torqe_total = Torqe_total+Torqe[j];
  }
  unsigned long currentMillis1 = millis();
  unsigned long currentMillis2 = millis();
  if (currentMillis2 - previousMillis1 >= interval1) {
    previousMillis1 = currentMillis2;
      float torque = Torqe_total;
      torque = torque/1000;
      
      sensorValues[currentIndex] = torque;
      currentIndex = (currentIndex + 1) % arraySize;
      float sum = 0;
      int validCount = 0;
      for (int i = 0; i < arraySize; i++) {
        if (sensorValues[i] > 0) {
          sum += sensorValues[i];
          validCount++;
        }
      }
      float mean = (validCount > 0) ? sum / validCount : 0;
      float sumSqDiff = 0;

      for (int i = 0; i < arraySize; i++) {
        if (sensorValues[i] > 0) {
          sumSqDiff += pow(sensorValues[i] - mean, 2);
        }
      }

      float stdDev = (validCount > 1) ? sqrt(sumSqDiff / (validCount - 1)) : 0;
     
 
      float e = 2.71828;
      float a = 1;
      float b = 0.0;
      float reX = pow(e, (-stdDev));

      // คำนวณค่า first และ second
      float first = a * (tanh(reX));
      float second = b * Hc[0];
     
      // บวกค่า first และ second แล้วเก็บใน Hc[1]
      Hc[1] = first + second;
       Serial.print(torque);
      Serial.print(" ");
      Serial.print(stdDev);
      Serial.print(" ");
      Serial.print(reX);
      Serial.print(" ");
      Serial.print(first);
      Serial.print(" ");
      Serial.print(second);
      Serial.print(" ");
      Serial.println(Hc[1]);
      // แสดงผลค่าปัจจุบัน
      // Serial.print("Hc: ");
      // Serial.print(Hc[0]);
      // Serial.print(" -> ");
      // Serial.print(Hc[1]);
      // Serial.println();

      // อัพเดท Hc[0] สำหรับการทำงานรอบต่อไป
      Hc[0] = Hc[1];
      speed = map(Hc[1], 1, 0, 1, 1000);
  }
/////////////////////////////////////////////////////////////

}

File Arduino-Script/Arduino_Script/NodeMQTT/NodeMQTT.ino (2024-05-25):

#include <WiFi.h>
#include "PubSubClient.h"
#include <ESP32Servo.h>
#define GPIO_PIN_1 2 
#define GPIO_PIN_2 15

const char* ssid = "GGOOGG";
const char* password = "0123456789";
const char* mqttServer = "broker.emqx.io";
int port = 1883;
String stMac;
char mac[50];
char clientId[50];

WiFiClient espClient;
PubSubClient client(espClient);
Servo ServoMouth;
Servo ServoNeck;
int randNgum=3;

void setup() {
  Serial.begin(115200);
  Serial.println(ssid);
  pinMode(GPIO_PIN_1, OUTPUT); // กำหนด GPIO เป็นโหมด OUTPUT
  pinMode(GPIO_PIN_2, OUTPUT);
  ServoMouth.attach(16);
  ServoNeck.attach(17);
  ServoMouth.write(0);
  ServoNeck.write(40);
  wifiConnect();
  Serial.println("");
  Serial.println("WiFi connected");
  Serial.println("IP address: ");
  Serial.println(WiFi.localIP());
  /*Serial.println(WiFi.macAddress());
  stMac = WiFi.macAddress();
  stMac.replace(":", "_");
  Serial.println(stMac);*/
  client.setServer(mqttServer, port);
  client.setCallback(callback);
}

void wifiConnect() {
  //WiFi.mode(WIFI_STA);
  WiFi.begin(ssid, password);
  while (WiFi.status() != WL_CONNECTED) {
    delay(500);
    Serial.print(".");
  }
}

void mqttReconnect() {
  while (!client.connected()) {
    Serial.print("Attempting MQTT connection...");
    long r = random(1000);
    sprintf(clientId, "clientId-%ld", r);
    if (client.connect(clientId)) {
      Serial.print(clientId);
      Serial.println(" connected");
      client.subscribe("ControGG");
    } else {
      Serial.print("failed, rc=");
      Serial.print(client.state());
      Serial.println(" try again in 5 seconds");
      delay(5000);
    }
  }
}

void callback(char* topic, byte* message, unsigned int length) {
  Serial.print("Message arrived on topic: ");
  Serial.print(topic);
  Serial.print(". Message: ");
  String stMessage;
  
  for (int i = 0; i < length; i++) {
    Serial.print((char)message[i]);
    stMessage += (char)message[i];
  }
  Serial.println();

  if (String(topic) == "ControGG") {
    Serial.print("Changing output to ");
    Serial.print(stMessage);
    
    if(stMessage == "Forward"){
    digitalWrite(GPIO_PIN_1, HIGH);
    }
    else if(stMessage == "Stop"){
   digitalWrite(GPIO_PIN_1, LOW);
    }
    else if(stMessage == "Eat"){
      digitalWrite(GPIO_PIN_1, LOW);
      randNgum = random(2,6);
      ngum(randNgum);
     digitalWrite(GPIO_PIN_1, HIGH);
    }
  }
}

void loop() {
  delay(10);
  if (!client.connected()) {
    mqttReconnect();
  }
  client.loop();
}

void ngum(int i)
{
  delay(1000);
  for(int posDegrees = 40; posDegrees >= 0; posDegrees--) {
    ServoNeck.write(posDegrees);
    delay(10);
  }
  for(int j = 0;j<=i;j++)
  {
    for(int posDegrees = 0; posDegrees <= 45; posDegrees++) {
    ServoMouth.write(posDegrees);
    delay(7);
    }
    for(int posDegrees = 45; posDegrees >= 0; posDegrees--) {
    ServoMouth.write(posDegrees);
    delay(7);
    }
  }
  delay(300);
  for(int posDegrees = 0; posDegrees <= 40; posDegrees++) {
    ServoNeck.write(posDegrees);
    delay(10);
  }
}

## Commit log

2024-05-19 Add Arduino Script that doesn't finish tuning
    [CPG-VRN.ino]
2024-05-21 Add lastest Arduino Script
2024-05-25 CPG and VRN graph that genarate in Exel
    [CPGandVRN-Graph.xlsx]
2024-05-26 add Hormone Excel Ref.
    [HormoneTired, connection, speed.xlsx]
2024-05-26 Delete CAD/File JPG directory
    delete jpg
2024-05-26 renamed: CAD/File step/Legs/Hind legs/Assembly Left.STEP -> CAD/File step/Legs/Rear legs/Assembly Left.STEP renamed: CAD/File step/Legs/Hind legs/Assembly Right.STEP -> CAD/File step/Legs/Rear legs/A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
    [Assembly Left.STEP, Assembly Right.STEP, back1.STEP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]
2024-05-27 new file: Node-RED flows/flows.json
2024-05-27 new file: CAD/File step/BODY/BODY_PART1.STEP new file: CAD/File step/BODY/BODY_PART2.STEP new file: CAD/File step/BODY/BODY_PART3.STEP new file: CAD/File step/BODY/BODY_PART4.STEP new file: CAD/File 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
    [BODY_PART1.STEP, BODY_PART2.STEP, BODY_PART3.STEP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]
